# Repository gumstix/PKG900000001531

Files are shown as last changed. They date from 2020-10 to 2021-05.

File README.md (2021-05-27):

# Gumstix Raspberry Pi CM4 + Pixhawk FMUv6
## PKG900000001531 

The **Gumstix Raspberry Pi CM4 + Pixhawk FMUv6** brings together 3 powerful compute devices.  With the Raspberry Pi CM4 module, the Google Coral TPU, and the ST Micro STM32F7 MCU, along with support hardware for MAVs, rovers and other robotics platforms,  designing TensorFlow-assisted autonomous vehicles has never been so accessible.

The *CM4 + Pixhawk FMUv6* is one of the first boards conforming to Pixhawk's v6 specification for Flight Management Units (FMUs), including on-board sensor bank, standard Pixhawk data and power connectors, octal PWM outputs, and firmware support.

The *CM4 + Pixhawk FMUv6* features single-connection programming and debugging.  Power the PCB, flash the CM4's MMC, program the FMU's frimware, or monitor their serial consoles from the same USB Type-C connection.

__Features Include__:
* Raspberry Pi CM4 connector
* Dual Raspberry Pi Camera connectors
* Serial console over USB
* USB Type-C power delivery
* STMicro STM32H753 MCU
* Pixhawk GPS, analog power, RC, and CAN connectors
* 8 PWM outputs
* On-board accelerometer, magnetometer and gyroscope
* On-board barometer
* ASMedia ASM1142 PCIe to USB3.1 controller
* Google Coral G313 TPU (via USB3)

__Links:__
* [AutoDoc Datasheet][autodoc]
* [Specifications][spec]
* [Store Page][store]
* [Schematics and Layout][hardware]

[thumbnail]: about:blank
[autodoc]: PKG900000001531_AutoDoc.pdf
[spec]: PKG900000001531_SpecSheet.pdf
[store]: https://store.gumstix.com/cm4-pixhawk6-mini/
[hardware]: hardware/hardware.md
[firmware]: firmware/firmware.md

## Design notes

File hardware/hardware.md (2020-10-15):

# Hardware

[Schematic PDF][pdf]
EAGLE [Schematic][sch] and [Layout][brd]

[pdf]: PKG900000001531.pdf
[brd]: PKG900000001531.brd
[sch]: PKG900000001531.sch

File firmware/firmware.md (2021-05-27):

# Firmware

## Raspberry Pi OS

* [Raspberry Pi OS (64-bit recommended)](https://downloads.raspberrypi.org/raspios_arm64/images/)
* Username: pi
* Password: raspberry
* Modifications: [config.txt:](config.txt)
```
    # pixhawk
    enable_uart=1
    dtoverlay=dwc2,dr_mode=host
    start_x=1
    gpu_mem=128
    dtoverlay=uart4,ctsrts
    dtoverlay=pcie-32bit-dma
    gpio=6,7=op,dh
```
* Download to /boot folder (first partition) to enable both cameras
    [dt-blob.bin](dt-blob.bin)

## ROS2 Integration

__PX4 Update__:
* Add micrortps client
  * [PX4 1.12.0](px4_fmu-v6u_rtps.px4)
  ```
    FW git-hash: db3c89b1e34af65efc334d928a82196947bd8a3a
    FW version: 1.12.0 80 (17563776)
    FW git-branch: master
  ```
  * Compile with [patch](0001-CM4-micrortps.patch)
  ```
    git am < 0001-CM4-micrortps.patch 
    make px4_fmu-v6u_rtps upload
  ```

__Raspberry Pi CM4 Update__:
* [Install Docker](https://docs.docker.com/engine/install/debian/)
* Add Non-Root User
  ```
    sudo usermod -aG docker ${USER}
  ```
* Enable Docker starting on boot
  ```
    sudo systemctl enable docker
  ```
* Get the image and make it start on boot
  ```
    docker run -d --privileged --net=host --platform=linux/arm64 --restart=always gumstix/px4_ros2
  ```

__[ROS 2 Offboard Control Example](https://docs.px4.io/master/en/ros/ros2_offboard_control.html)__
* Run Docker image on another device on network (can be done on CM4 on Pixhawk).
  * Desktop machine
    ```
      docker run -it --net=host --platform=linux/amd64 gumstix/px4_ros2 bash
    ```
  * Raspberry Pi CM4
    ```
      docker run -it --net=host --platform=linux/arm64 gumstix/px4_ros2 bash
    ```
* Run offboard control example (ros2 is already sourced)
  ```
    ros2 run px4_ros_com offboard_control
  ```

## Coral Accelerator Example
* Install Docker - See above
* Execute steps [1](https://coral.ai/docs/accelerator/get-started/#1-install-the-edge-tpu-runtime), [2](https://coral.ai/docs/accelerator/get-started/#2-install-the-pycoral-library) and [3](https://coral.ai/docs/accelerator/get-started/#3-run-a-model-on-the-edge-tpu) of the [Coral Getting Started](https://coral.ai/docs/accelerator/get-started/)
* Step 3 needs to be run every time before docker command below
* Run gstreamer on host device (ip address = w.x.y.z)
```
  gst-launch-1.0 udpsrc port=5000 ! application/x-rtp,encoding-name=H264,payload=96 ! rtph264depay ! decodebin ! autovideosink
```
* Run Docker image and stream to host device
```
  docker run -d --privileged --network=host gumstix/coral_camera --hostip w.x.y.z
```

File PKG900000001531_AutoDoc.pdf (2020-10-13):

# CM4 Pixhawk 6 Mini

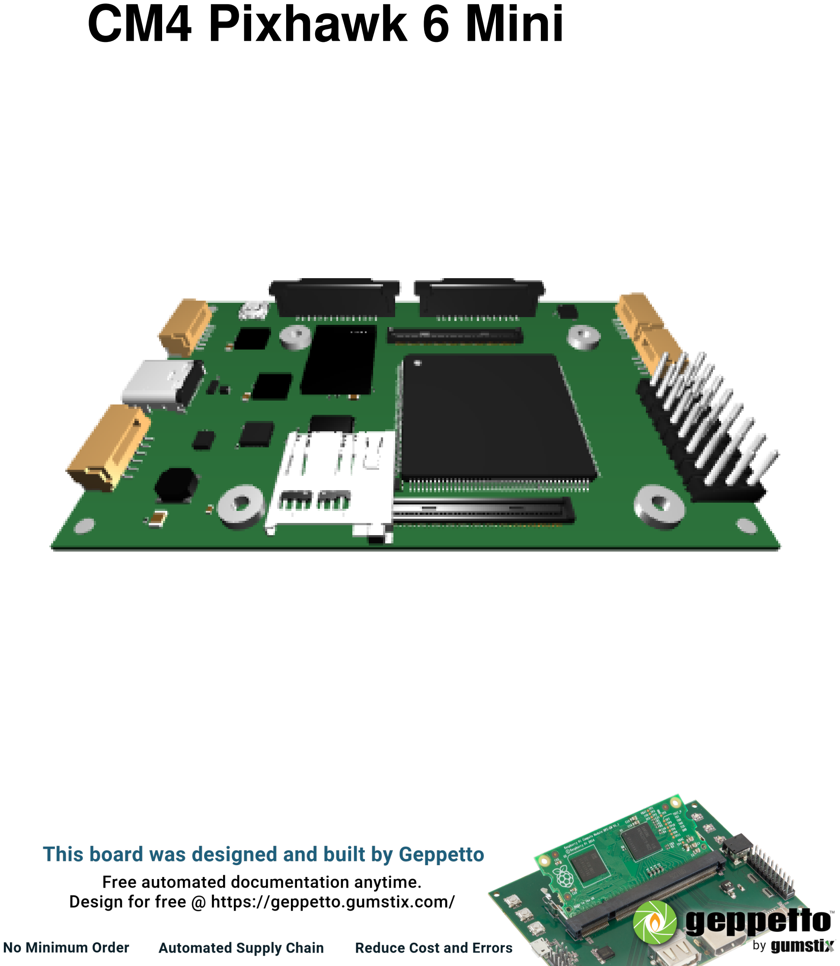
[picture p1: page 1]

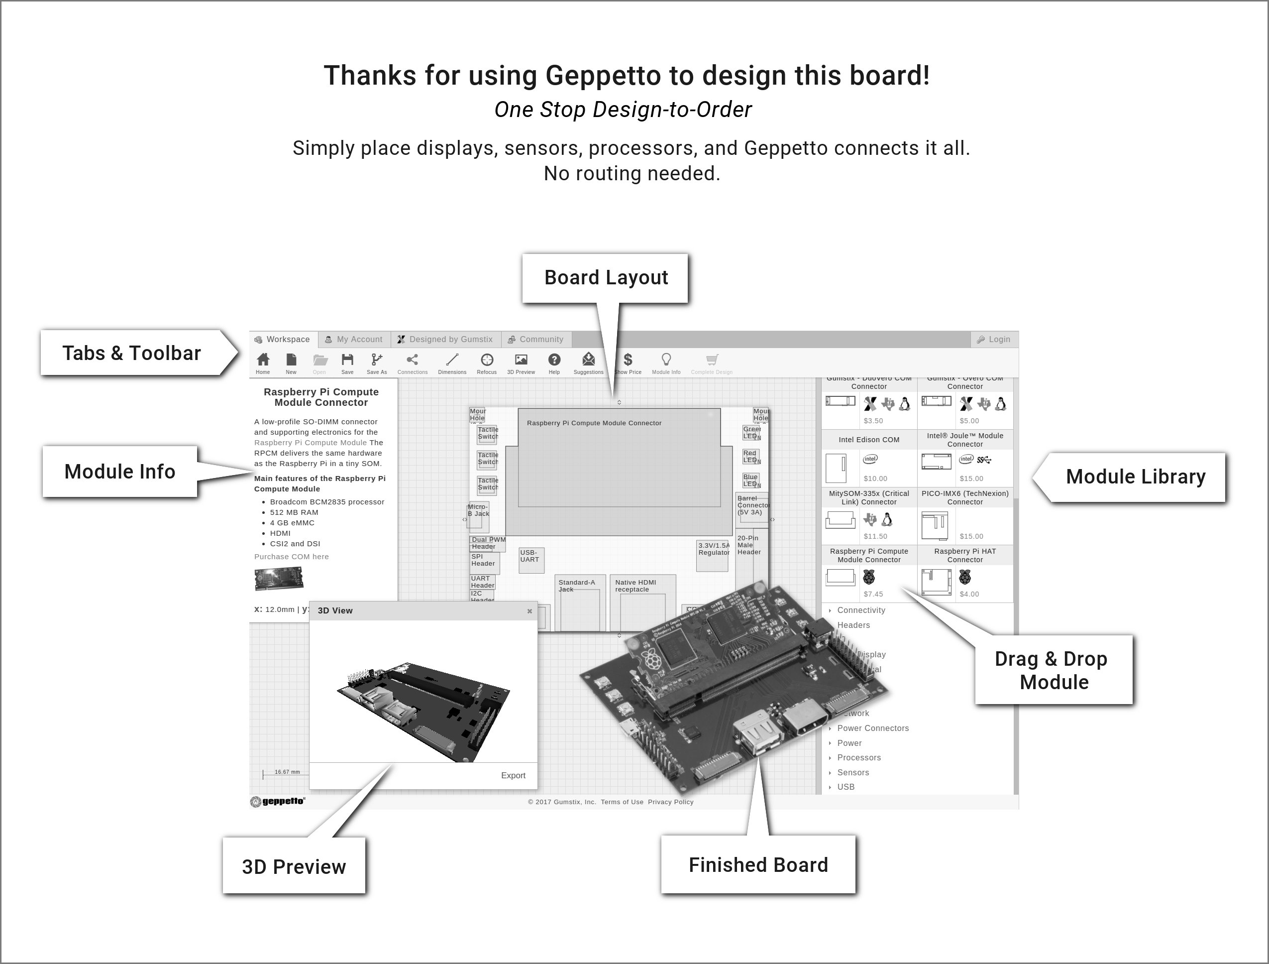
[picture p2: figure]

Gumstix, Inc. shall have no liability of any kind, express or implied, arising out of the use of the Information in this document, including direct, indirect, special or consequential damages.

Gumstix, Inc. may have patents, patent applications, trademarks, copyrights, trade secrets or other intellectual property rights pertaining to Gumstix products described in this document (collectively ”Gumstix Intellectual Property”).

Except as expressly provided in any written license or agreement from Gumstix, Inc., this document and the information contained therein does not create any license to Gumstix’s Intellectual Property.

The Information contained herein is subject to change without notice. Revisions may be issued regarding changes and/or additions.

Copyright

c 2020, Gumstix, Inc. All rights reserved.

## Board Description

Uses Raspberry Pi CM4 Connector as its COM/processor.

Functional modules include:
USB Type-C PD (5V)
3-Port USB Client Hub
USB-UART
USB-UART
USB Type-C PD (5V)
HART Bridge

## Board Dimensions

8cm x 5cm

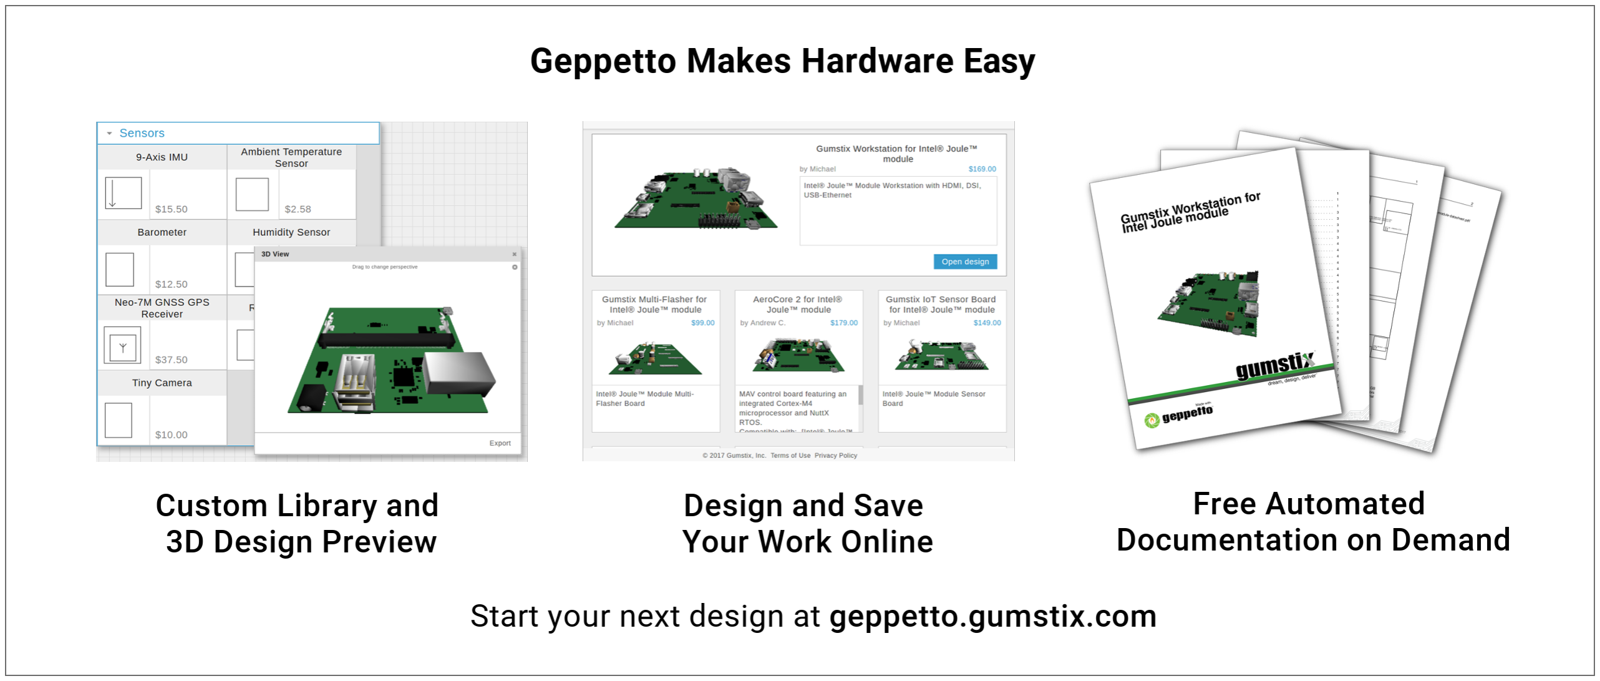
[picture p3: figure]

i

## Contents

1 Modules on Board | 1

ii

CM4 Pixhawk 6 Mini | iii
2 Module Connections Graph | 9
3 Module Power Graph | 10

Revised September 28, 2020

CM4 Pixhawk 6 Mini | 1

## 1 Modules on Board

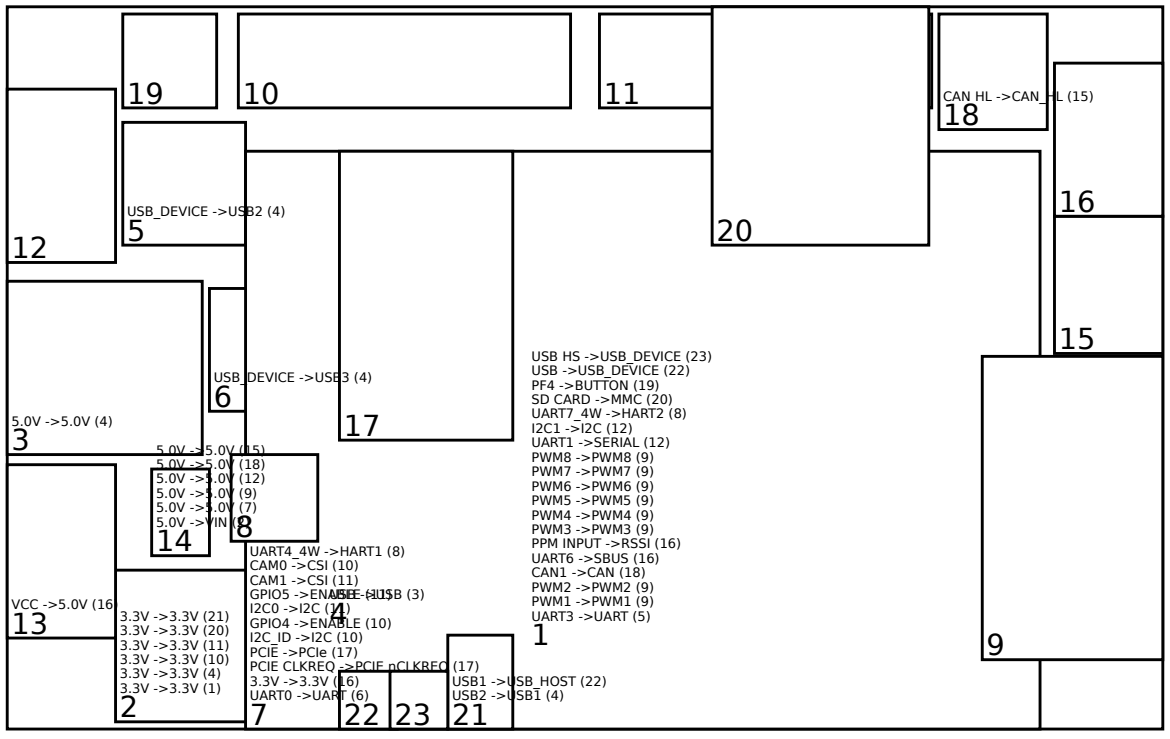
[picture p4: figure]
UART3 ->UART (5); PWM1 ->PWM1 (9); PWM2 ->PWM2 (9); CAN1 ->CAN (18); UART6 ->SBUS (16); PPM INPUT ->RSSI (16); PWM3 ->PWM3 (9); PWM4 ->PWM4 (9); PWM5 ->PWM5 (9); PWM6 ->PWM6 (9); PWM7 ->PWM7 (9); PWM8 ->PWM8 (9); UART1 ->SERIAL (12); UART7_4W ->HART2 (8); SD CARD ->MMC (20); PF4 ->BUTTON (19); USB ->USB_DEVICE (22); USB HS ->USB_DEVICE (23); USB ->USB (3); USB_DEVICE ->USB2 (4); USB_DEVICE ->USB3 (4); UART0 ->UART (6); PCIE CLKREQ ->PCIE nCLKREQ (17); PCIE ->PCIe (17); GPIO4 ->ENABLE (10); GPIO5 ->ENABLE (11); CAM1 ->CSI (11); CAM0 ->CSI (10); UART4_4W ->HART1 (8); VCC ->5.0V (16); 5.0V ->VIN (2); CAN HL ->CAN_HL (15); USB2 ->USB1 (4); USB1 ->USB_HOST (22)

3.3V ->3.3V (21) 3.3V ->3.3V (20) 3.3V ->3.3V (11) 3.3V ->3.3V (10) 3.3V ->3.3V (4) 3.3V ->3.3V (1) 2 | 7

### 1.1 Processors

### 1.1.1 PX4 FMUv6 (v1) (1)

PX4 FMUv6

STM32H753IIT6 is a 32-bit Arm Cortex-M7 core with double precision FPU and L1 cache: 16 Kbytes of data and 16 Kbytes of instruction cache; frequency up to 480 MHz, MPU, 1027 DMIPS/ 2.14 DMIPS/MHz (Dhrystone 2.1), and DSP instructions. It has 2 Mbytes of Flash memory and 1 Mbyte of RAM. Requires:

- 3.3V from 3.3V/1.5A Regulator (2)

Provides:

- UART3 to USB-UART (5)
- PWM1 to Octal PWM Header (9)
- PWM2 to Octal PWM Header (9)
- CAN1 to NXP TJA1051TK/3 CAN Transceiver (18)
- UART6 to Pixhawk RC Input (16)

- PPM INPUT to Pixhawk RC Input (16)
- PWM3 to Octal PWM Header (9)
- PWM4 to Octal PWM Header (9)
- PWM5 to Octal PWM Header (9)
- PWM6 to Octal PWM Header (9)
- PWM7 to Octal PWM Header (9)
- PWM8 to Octal PWM Header (9)
- UART1 to Pixhawk Basic GPS (12)
- I2C1 to Pixhawk Basic GPS (12)
- UART7 4W to HART Bridge (8)
- SD CARD to microSD slot (20)
- PF4 to Tactile Switch (19)
- USB to USB Bridge (22)
- USB HS to USB Bridge (23)

### 1.2 Power

1.2.1 3.3V/1.5A Regulator (v21) (2)

This DC to DC step down regulator provides a 3.3V DC output at 1.5A needed by certain components on this board. It is capable of accepting an input voltage between 3.1 to 16V DC and output is controlled by the TI TPS6211 buck regulator.
It recieves VIN from TI TPS2121 Power Mux (14).

The datasheet for the TPS6211 regulator is available at:

http://www.ti.com/lit/ds/symlink/tps62110.pdf

This regulator provides 3.3V to:

- PX4 FMUv6 (1)
- 3-Port USB Client Hub (4)
- Raspberry Pi Vertical Camera Connector (10)
- Raspberry Pi Vertical Camera Connector (11)
- microSD slot (20)
- USB 2-Port Switch (21)

### 1.2.2 TI TPS2121 Power Mux (v3) (14)

The TI TPS2121 power muxer module transitions between two power sources seamlessly. The au-toswitching power multiplexer ensures power is delivered from the connected source with the highest voltage.

The TPS2121 datasheet is available at:

http://www.ti.com/lit/ds/symlink/tps2121.pdf

This module is not connected.

### 1.3 USB

### 1.3.1 USB Type-C PD (5V) (v1) (3)

A USB Type-C port allows your design to connect as a USB 2.0 and provides up to 3A @ 5.0V.

This port is connected to USB on 3-Port USB Client Hub (4).

1.3.2 3-Port USB Client Hub (v7) (4)

The 3-port USB client hub module offers three interfaces for on-board USB client devices to a single USB device port using the Microchip USB2513 USB 2.0 Hi-speed Hub Controller.

The datasheet for the USB2513 IC is available at:

http://ww1.microchip.com/downloads/en/DeviceDoc/00001692C.pdf

The USB client hub links: USB on USB Type-C PD (5V) (3);
to the following USB device ports:
- USB DEVICE on USB-UART (5)
- USB DEVICE on USB-UART (6)
- USB2 on USB 2-Port Switch (21)

### 1.3.3 USB 2-Port Switch (v1) (21)

USB 2-Port Switch allows the sharing of a single USB 2.0 port.

It requires:

- 3.3V from 3.3V/1.5A Regulator (2)

It provides the following outputs:

- USB2 to 3-Port USB Client Hub (4)
- USB1 to USB Bridge (22)

### 1.4 Converters

### 1.4.1 USB-UART (v21) (5)

Also known as an FTDI, this USB to UART converter allows a USB connection to the board to be-have as a virtual RS232 serial connection. It offers direct and complete access to the system from a development machine by way of the FTDI FT232RQ USB – UART IC.

Technical documentation for the FT232RQ is available at:

http://www.ftdichip.com/Support/Documents/DataSheets/ICs/DS_FT232R.pdf

This USB to UART converter connects a host machine from 3-Port USB Client Hub (4) to UART3 on PX4 FMUv6 (1).

### 1.4.2 USB-UART (v21) (6)

Also known as an FTDI, this USB to UART converter allows a USB connection to the board to be-have as a virtual RS232 serial connection. It offers direct and complete access to the system from a development machine by way of the FTDI FT232RQ USB – UART IC.

Technical documentation for the FT232RQ is available at:

http://www.ftdichip.com/Support/Documents/DataSheets/ICs/DS_FT232R.pdf

This USB to UART converter connects a host machine from 3-Port USB Client Hub (4) to UART0 on Raspberry Pi CM4 Connector (7).

### 1.4.3 HART Bridge (v1) (8)

A HART-HART bridge interfaces two modules with hardware controlled UART lines (e.g., interfacing two processors).

This HART bridge connects UART4 4W on Raspberry Pi CM4 Connector (7) to UART7 4W on PX4 FMUv6 (1).

### 1.4.4 NXP TJA1051TK/3 CAN Transceiver (v2) (18)

The TJA1051TK/3 is a high-speed CAN transceiver that provides an interface between a controller Area Network (CAN) protocol controller and the physical two-wire CAN bus. The transceiver is designed for high-speed CAN applications in the automotive industry, providing differential transmit and receive capability to (a microcontroller with) a CAN protocol controller. The TJA1051TK3 implements the CAN physical layer as defined in ISO 11898-2:2016 and SAE J2284-1 to SAE J2284-5. This implementation enables reliable communication in the CAN FD fast phase at data rates up to 5 Mbit/s. It is suitable for 12 V and 24 V systems. The operating supply voltage of the transceiver is between 4.5V and 5.5V. The module supports IO logic levels of either 3.3V or 5.0V between the controller and transceiver based on the user’s selection while designing on geppetto.

TJA1051TK/3 datasheet:

https://www.nxp.com/docs/en/data-sheet/TJA1051.pdf

This module is connected to CAN1 on PX4 FMUv6 (1).

This module provides the following outputs:

- CAN HL to CAN HL on Pixhawk CAN (15)

### 1.5 COM Connectors

### 1.5.1 Raspberry Pi CM4 Connector (v4) (7)

The Raspberry Pi Compute Module 4 (RPCM4) module contains two connectors to interface with the RPCM4 device. The RPCM4 COM connector is ONLY compatible with the RPCM4.

Technical details for the RPCM modules can be found at:

https://www.raspberrypi.org/documentation/hardware/computemodule/datasheet.md

It requires:

- 5.0V from TI TPS2121 Power Mux (14)

The Geppetto Pi Compute 4 connector provides the following outputs:

- UART0 to USB-UART (6)
- 3.3V to Pixhawk RC Input (16)
- PCIE CLKREQ to Google Coral G313-06329-00 Accelerator (17)
- PCIE to Google Coral G313-06329-00 Accelerator (17)
- I2C ID to Raspberry Pi Vertical Camera Connector (10)
- GPIO4 to Raspberry Pi Vertical Camera Connector (10)
- I2C0 to Raspberry Pi Vertical Camera Connector (11)
- GPIO5 to Raspberry Pi Vertical Camera Connector (11)
- CAM1 to Raspberry Pi Vertical Camera Connector (11)
- CAM0 to Raspberry Pi Vertical Camera Connector (10)
- UART4 4W to HART Bridge (8)

### 1.6 Motors and Relays

### 1.6.1 Octal PWM Header (v11) (9)

This module offers eight PWM headers for controlling servo motors and other PWM-controlled devices.

This header offers PWM outputs connected to:

- PWM1 to PWM1 on PX4 FMUv6 (1)
- PWM2 to PWM2 on PX4 FMUv6 (1)

- PWM3 to PWM3 on PX4 FMUv6 (1)
- PWM4 to PWM4 on PX4 FMUv6 (1)
- PWM5 to PWM5 on PX4 FMUv6 (1)
- PWM6 to PWM6 on PX4 FMUv6 (1)
- PWM7 to PWM7 on PX4 FMUv6 (1)
- PWM8 to PWM8 on PX4 FMUv6 (1)
- 5.0V to 5.0V on TI TPS2121 Power Mux (14)

### 1.7 Connectors (Signal)

### 1.7.1 Raspberry Pi Vertical Camera Connector (v6) (10) — CAM0

The Raspberry Pi Vertical camera connector module is a 15-pin ribbon connector that exposes a 2-lane MIPI camera system to an external high-resolution camera module.

The CSI port is connected to CAM0 on Raspberry Pi CM4 Connector (7).

I2C communication is connected to I2C ID on Raspberry Pi CM4 Connector (7).

ENABLE input provided by GPIO4 on Raspberry Pi CM4 Connector (7).

### 1.7.2 Raspberry Pi Vertical Camera Connector (v6) (11) — CAM1

The Raspberry Pi Vertical camera connector module is a 15-pin ribbon connector that exposes a 2-lane MIPI camera system to an external high-resolution camera module.

The CSI port is connected to CAM1 on Raspberry Pi CM4 Connector (7).

I2C communication is connected to I2C0 on Raspberry Pi CM4 Connector (7).

ENABLE input provided by GPIO5 on Raspberry Pi CM4 Connector (7).

### 1.7.3 USB Bridge (v9) (22)

The USB bridge connects PX4 FMUv6 (1) to USB 2-Port Switch (21) as a USB device.

### 1.7.4 USB Bridge (v9) (23)

The USB bridge connects PX4 FMUv6 (1) to as a USB device.

### 1.8 Custom Modules

### 1.8.1 Pixhawk Basic GPS (v3) (12)

The custom 6-pin JST GH header offers up to 6 pins that can be used at the customer’s discretion.

This module has the following connections:

- SERIAL to UART1 from PX4 FMUv6 (1)
- I2C to I2C1 from PX4 FMUv6 (1)
- 5.0V to 5.0V from TI TPS2121 Power Mux (14)

### 1.8.2 Pixhawk Analog Power (v3) (13)

The custom 6-pin JST GH header offers up to 6 pins that can be used at the customer’s discretion.

This module is not connected.

### 1.8.3 Pixhawk CAN (v6) (15)

The custom 4-pin JST GH header offers up to 4 pins that can be used at the customer’s discretion.

This module has the following connections:

- 5.0V to 5.0V from TI TPS2121 Power Mux (14)
- CAN HL to CAN HL from NXP TJA1051TK/3 CAN Transceiver (18)

•

### 1.8.4 Pixhawk RC Input (v4) (16)

The custom 5-pin JST GH header offers up to 5 pins that can be used at the customer’s discretion.

This module has the following connections:

- SBUS to UART6 from PX4 FMUv6 (1)
- RSSI to PPM INPUT from PX4 FMUv6 (1)
- 3.3V to 3.3V from Raspberry Pi CM4 Connector (7)
- 5.0V to VCC from Pixhawk Analog Power (13)

### 1.9 Sensors

### 1.9.1 Google Coral G313-06329-00 Accelerator (v2) (17)

The Google Coral Accelerator Module is a multi-chip module (MCM) that includes the Edge TPU and its own power control. The Edge TPU is a small ASIC designed by Google that accelerates Tensor

Flow Lite models using little power: it’s capable of performing 4 trillion operations per second (4 TOPS), using 2 watts of powerthat’s 2 TOPS per watt. For example, it can execute state-of-the-art mobile vision models such as MobileNet v2 at almost 400 frames per second, in a power efficient manner. This on-device ML processing reduces latency, increases data privacy, and removes the need for a constant internet connection. The module provides either of the host interface i.e. PCIe Gen2 x 1 or USB2.0.

The datasheet for the G313-06329-00 module is available at:

https://coral.ai/static/files/Coral-Accelerator-Module-datasheet.pdf

The module connects to the following buses:

- PCIE nCLKREQ to PCIE CLKREQ on Raspberry Pi CM4 Connector (7)
- VLOGIC PCIE CTRL to VLOGIC on Raspberry Pi CM4 Connector (7)
- PCIe to PCIE on Raspberry Pi CM4 Connector (7)

•

### 1.10 Lights and Switches

### 1.10.1 Tactile Switch (v22) (19) — RESET

This 4.9 sq. mm pull-down touch switch provides a user input for the signal PF4 on PX4 FMUv6 (1).

### 1.11 Memory

### 1.11.1 microSD slot (v16) (20)

The Micro SD card slot module provides removable non-volatile memory to Geppetto designs.

The SD card reader is connected to SD CARD on PX4 FMUv6 (1).

## 2 Module Connections Graph

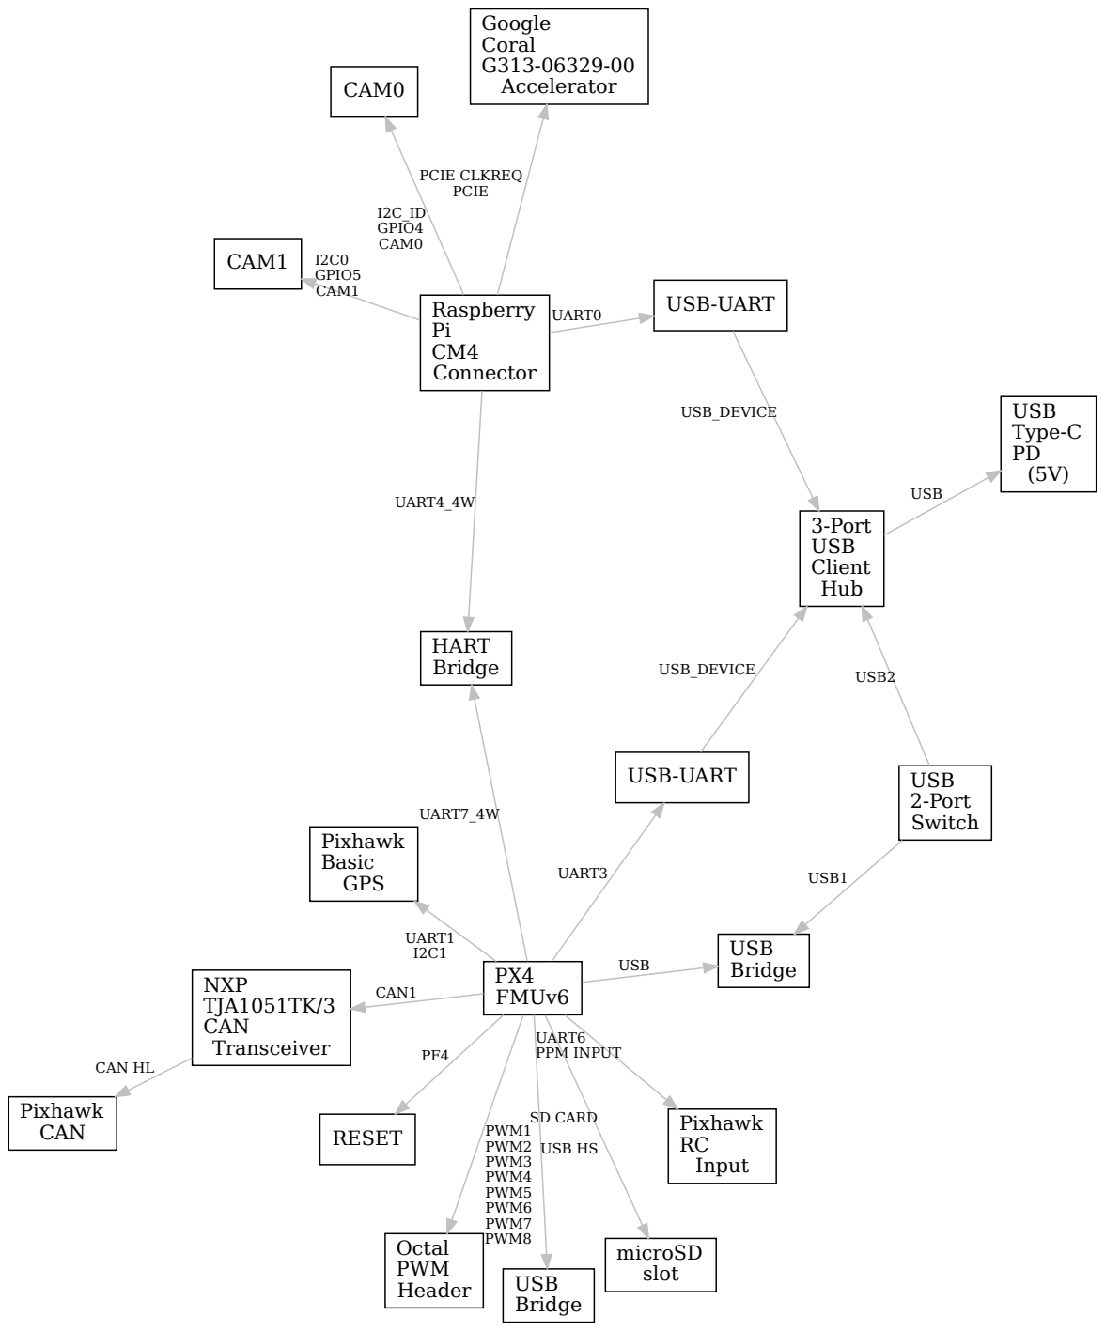
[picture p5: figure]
PX4 FMUv6; USB-UART; UART3; Octal PWM Header; PWM1 PWM2 PWM3 PWM4 PWM5 PWM6 PWM7 PWM8; NXP TJA1051TK/3 CAN Transceiver; CAN1; Pixhawk RC Input; UART6 PPM INPUT; Pixhawk Basic GPS; UART1 I2C1; HART Bridge; UART7_4W; microSD slot; SD CARD; RESET; USB Bridge USB; USB Bridge; USB HS; 3-Port USB Client Hub; USB_DEVICE; Pixhawk CAN; CAN HL; USB Type-C PD (5V); USB; USB 2-Port Switch; USB1; USB2; Raspberry Pi CM4 Connector; UART4_4W; UART0; Google Coral G313-06329-00 Accelerator; PCIE CLKREQ PCIE; CAM0; I2C_ID GPIO4 CAM0; CAM1; GPIO5 CAM1

Figure 1: excludes power modules

## 3 Module Power Graph

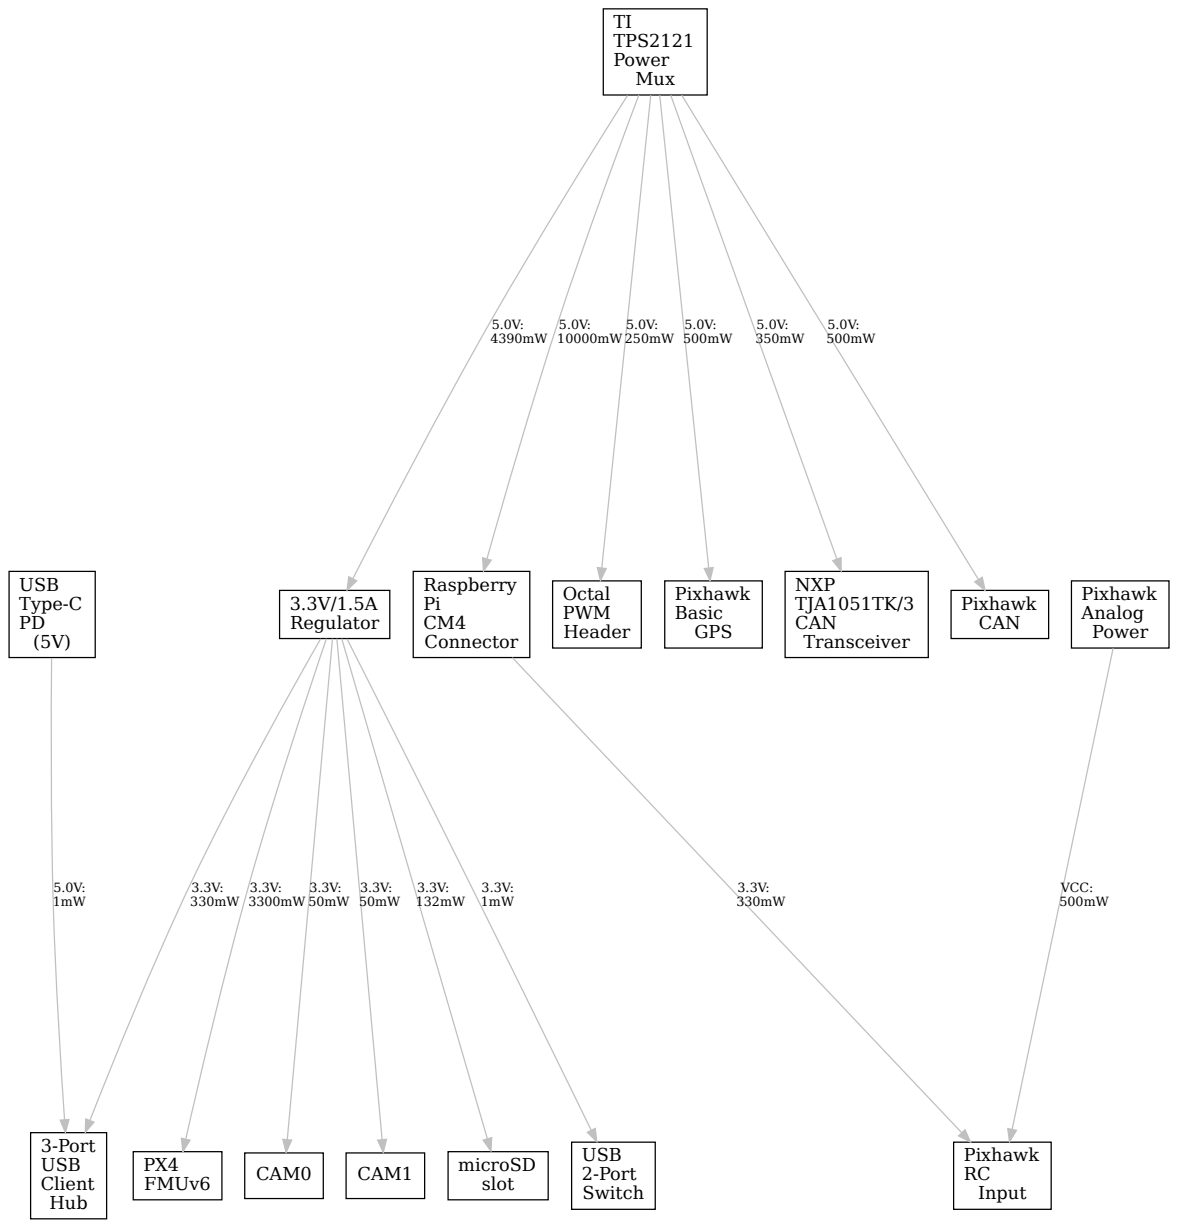
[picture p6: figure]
3.3V/1.5A Regulator; PX4 FMUv6; 3-Port USB Client Hub; CAM0; CAM1; microSD slot; USB 2-Port Switch; TI TPS2121 Power Mux; Raspberry Pi CM4 Connector; Octal PWM Header; Pixhawk Basic GPS; NXP TJA1051TK/3 CAN Transceiver; Pixhawk CAN; USB Type-C PD (5V); Pixhawk RC Input; Pixhawk Analog Power; VCC: 500mW

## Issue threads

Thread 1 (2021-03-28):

Flashing the CM4

nilay994, 2021-03-28:
Thanks for the nice board @Gumstix!

Questions related to getting started with the Gumstix Raspberry Pi CM4:

1. Can the eMMC of CM4 be flashed directly after being mounted to the Gumstix Board? In other words, can the USB-C connector of the gumstix disable the eMMC boot and force the RPi to boot in the flashing mode?
2. I see "This USB to UART converter connects a host machine from 3-Port USB Client Hub (4) to UART0 on Raspberry Pi CM4 Connector (7)." Is this dependent on the three positions that a switch can be in, next to the USB hub? The USB hub looks really nice, since it exposes multiple UARTs of the STM and RPi at one port. Could there be more verbose statements about the USB hub? Would love to be able to use this multi-channel functionality more frequently.
3. Can there be more verbose documentation of the connection between the STM32 and the CM4? Are these interfaces completely accessible to the user? or are they locked by some application running on the CM4?
4. What is the difference between the RPi image provided [here](https://github.com/gumstix/PKG900000001531/blob/master/firmware/firmware.md) and the default image? Is it just the device tree reference file?

patrickpoirier51, 2021-03-28:
Hello,

Funny, I received the board last week and stated working on this by the time you opened issue :-)...
I loaded the UBUNTU image using the Compute Module IO board and it worke flawlessly.
It is mapping  a com port on the USB c and output MAVLINK @ 57600bps

Hope it helps

smithandrewc, 2021-03-30:
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
Not on this version.  We're building a new version of the board that will allow this.

> 2. I see "This USB to UART converter connects a host machine from 3-Port USB Client Hub (4) to UART0 on Raspberry Pi CM4 Connector (7)." Is this dependent on the three positions that a switch can be in, next to the USB hub? The USB hub looks really nice, since it exposes multiple UARTs of the STM and RPi at one port. Could there be more verbose statements about the USB hub? Would love to be able to use this multi-channel functionality more frequently.
This puts module puts out the default (UART0) console through an FTDI USB-UART port and is connected to the USB hub, accessible through the Type-C connector.  No switches are necessary, the CM4 console, FMU console and FMU USB bus are all available through the Type-C connector.
> 3. Can there be more verbose documentation of the connection between the STM32 and the CM4? Are these interfaces completely accessible to the user? or are they locked by some application running on the CM4?
The schematic for the board is available here, what additional documentation do you require?  The CM4 and STM32 are connected through a UART channel only (the default TELEM2 channel on FMU).
> 4. What is the difference between the RPi image provided [here](https://github.com/gumstix/PKG900000001531/blob/master/firmware/firmware.md) and the default image? Is it just the device tree reference file?
What "default image" are you referring to?

nilay994, 2021-03-31:
> The CM4 and STM32 are connected through a UART channel only (the default TELEM2 channel on FMU).

The USB-C hub is nice and versatile :) Found the channel in the schematics pdf, thank you for providing the reference. Planning to tap into these UART lines serving as a test point, can solder wires on to the 0R resistor.

> What "default image" are you referring to?

I could have been clearer. With default image, I meant the Raspberry Pi OS/Raspbian or the image that RPi flashing tool uses for getting started with the CM4.

Closed 2021-04-05.

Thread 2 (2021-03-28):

UBUNTU source & framework

patrickpoirier51, 2021-03-28:
Hello,

I just loaded the UBUNTU image and it work ok with PX4.

My goal is to make an image for ArduPilot and not wanting to reinvent the wheel, I would need detailled information on the different modules used (if any), specific mappings of peripherals, config files and startup scripts.

Regards

patrickpoirier51, 2021-03-29:
Well... in the meantime I think I'll dig into it ;-)

--First issue Pi is not showing on third USB mapping

I could see Mavlink on first USB and PX4 Shell on second USB, but no RPI login on third.
Her's what I dis to correct:

`/boot/firmware/config.txt
enable_uart=1

/boot/firmware/syscfg.txt
#cmdline=cmdline.txt
cmdline=cmdline.txt.serial

at cmdline.txt.serial
net.ifnames=0 dwc_otg.lpm_enable=0 console=serial0,115200 console=tty1 root=LABEL=writable rootfstype=ext4 elevator=deadline rootwait fixrtc

remove symlink on rc.local == I want a direct link to the port
cat rc.local
#!/bin/bash
#ln -s /dev/ttyAMA1 /dev/ttyS0
`

--

Then ENABLE WIFI
ENABLE WIFI
https://linuxconfig.org/ubuntu-20-04-connect-to-wifi-from-command-line

ENABLE SSH
https://linuxize.com/post/how-to-enable-ssh-on-ubuntu-20-04/

reboot then  ssh ubuntu on WIFI address  with raspberry as password

now we have access to internet and  we can update , add tools ... whatever
 !!! Issue while building packages =
`update-initramfs: Generating /boot/initrd.img-5.4.0-1021-raspi
Unsupported platform.
run-parts: /etc/initramfs/post-update.d//flash-kernel exited with return code 1
dpkg: error processing package initramfs-tools (--configure):
 installed initramfs-tools package post-installation script subprocess returned error exit status 1
Errors were encountered while processing:
 initramfs-tools
`

But the installed packages seems to work ok ... so far :-)

Finally install MAVPROXY

Install MAVPROXY
pip install PyYAML mavproxy --user

echo "export PATH=$PATH:$HOME/.local/bin" >> ~/.bashrc
source ~/.bashrc

 mavproxy.py --master=/dev/ttyAMA1 --baudrate=921600 --out=udpout: "toGCS:14550

Enjoy,  Regards

smithandrewc, 2021-03-29:
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

Autopilot was built to conform to Pixhawk FMUv6U standard. Spec should have been published by now but I don't see it. All board support has been added to mainline PX4. All hardware documents have been uploaded here.

What else are you looking for?

smithandrewc, 2021-03-29:
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

I believe only change required to get console is setting enable_uart=1.

Have you tried mainline Raspberry Pi OS? That works as well.

patrickpoirier51, 2021-03-29:
Hello,

Thanks for getting back so rapidly :-)

Concerning uart access , is this mapping  really required then ?
ln -s /dev/ttyAMA1 /dev/ttyS0

Has the mainline Raspberry Pi OS has access to the CORAL chip ?

Regards,

smithandrewc, 2021-03-29:
I don't see why that mapping would be required.

Coral chip is USB, software support is identical to USB Accelerator

https://coral.ai/docs/accelerator/get-started/

patrickpoirier51, 2021-03-29:
Ahhh cool , I thought it was deeply interconnected with GPIOS as described here:
**Gumstix Raspberry Pi CM4 + Pixhawk FMUv6   page 8**

The module connects to the following buses:
• PCIE nCLKREQ to PCIE CLKREQ on Raspberry Pi CM4 Connector (7)
• VLOGIC PCIE CTRL to VLOGIC on Raspberry Pi CM4 Connector (7)
• PCIe to PCIE on Raspberry Pi CM4 Connector (7)

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

patrickpoirier51, 2021-03-29:
and lsusb doe not show much

Bus 001 Device 001: ID 1d6b:0002 Linux Foundation 2.0 root hub
ubuntu@ubuntu:~$ Bus 001 Device 001: ID 1d6b:0002 Linux Foundation 2.0 root hub

patrickpoirier51, 2021-03-30:
OK, double check with schematic and yeah.... it is USB only

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

patrickpoirier51, 2021-03-30:
@smithandrewc  I think the documentation would  need to be more explicit....
Now question: How do we access the TPU ?

patrickpoirier51, 2021-03-30:
I cannot see the Google Coral on the Gumstix
It works OK on the CM IO Board with a CORAL stick plugged in USB

Any guidance ?

smithandrewc, 2021-03-30:
Early test boards had an issue with the Coral device, we've addressed it in our newest build.

patrickpoirier51, 2021-03-30:
@smithandrewc  there are other issues in this thread, I guess you will fix that ?

One other thing
it looks like you somehow installed an older version of tflite_runtime, the version should have returned 2.5:
python3 -c 'print(__import__("tflite_runtime").__version__)'
2.5.0

sudo pip3 remove tflite-runtime == it was 2.1
and reinstall with apt

smithandrewc, 2021-03-30:
What other issues? This Ubuntu image is the original one we deployed with the CM4 before there was mainline support. I would recommend using a new image. We will be removing this image soon.

patrickpoirier51, 2021-03-31:
The nonexistent  mapping of the Pi  console on USB
The outdated python library
The misguiding documentation

An I might add
The undocumented method to flash the firmware
The lack of transparence on a major issue with the Beta Units....

Le mar. 30 mars 2021 à 19:12, Andrew C. Smith ***@***.***> a
écrit :

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

patrickpoirier51, 2021-03-31:
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

This is misleading as the final design is purely USB

smithandrewc, 2021-03-31:
> I mean flashing the firmware on the STM32

This is a mainline supported PX4 board.  Flashing it follows the same routine as all the other PX4 boards (QGroundcontrol or via source code).

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

This is a good point, that is confusing.  We'll fix it, thanks for pointing it out.

patrickpoirier51, 2021-03-31:
You are welcome :-)

Closed 2021-03-30.

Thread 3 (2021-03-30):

USB Lines Criss-Cross Fix is not Working

patrickpoirier51, 2021-03-30:
The Coral chip is not detected on my Gumstix Raspberry Pi CM4 + Pixhawk FMUv6.

After having exhausted all the software and configuration issues, I decided to test on the CM4 IO board with my own Coral USB stick and all worked OK.

This is when I decided to investigate this hardware rework on the USB lines
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

Being a criss-cross it appear that the runs had to be cut.... and its not the case.
So I cut them:
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

Now I can see the USB device:
dmesg | grep usb
New USB device found, idVendor=1d6b, idProduct=0002, bcdDevice= 5.04
lsusb
Bus 001 Device 002: ID 1a6e:089a Global Unichip Corp.
Bus 001 Device 001: ID 1d6b:0002 Linux Foundation 2.0 root hub

But when I launch the test , the python test start but it never finalise the test  with sporadic bus speed errors messages on terminal.

Conclusion: This quick fix does not work properly as it expose and unbalance the USB data lines.

patrickpoirier51, 2021-04-15:
Hello,  When are yyou planning to release the new boards sowe can finish the ArduPilot integration ?

smithandrewc, 2021-04-15:
We're building a new version now. However, it is only making changes to the CM4 and Coral. How does this affect Ardupilot?

patrickpoirier51, 2021-04-15:
I am taking part of the CM4 integration, so I need a fully functionnal unit in order to build a complete image.

smithandrewc, 2021-04-16:
Well unfortunately due to scarcity of parts, I don't expect us to have a decent volume of these for a couple of months.  I would recommend you get a hold of an external USB coral device and CM4 board and do whatever testing you can.

Alternatively, you get get one of our Uprev AI and CM Robo boards
https://www.gumstix.com/cm4-uprev-ai.html
https://www.gumstix.com/cm-robo.html
Put the CM4 on the Uprev AI and into the Robo board end either connect the UART header on the Robo to GPS header on the Pixhawk or use the USB ports on the two boards.  It'll require some minor changes to get the MAVLink data on those channels but would get you as close as possible to the finished board.  If you're interested in pursuing either avenue, get a hold of our customer support.

mariorra, 2021-08-17:
Hi Guys! Thanks for sharing this issue

I arrive here bc I'm working on a solution that provides something similar. But let see that it is something there that makes me confuse.
The Version that I have is the 4. There the schematic shows the following connection. I wrote by hand the red lines to define what was the issue in the past.

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

My confusion is if I follow the connection between the ASM1142 and CORAL:

ASM1142                     LABEL                             LABEL             CORAL
USB1_SSTX_P PIN42    USB1_SSTX_P   -->    USB1_SSTX_N   PCIE_RX_P
USB1_SSTX_N PIN43   USB1_SSTX_N  -->     USB1_SSTX_P    PCIE_RX_N

Is the issue fixed on the side of the labels?
Do I have to follow the labels in order to have a good connection using the guidelines that google provides?

Thanks in advance

smithandrewc, 2021-08-17:
The initial post in this thread was in regards to the error in swapping the polarity of the USB2 signals.  That has been fixed.  Your question about swapping the polarity of the SSTX lines is intentional.  The superspeed signals allow for polarity inversion to allow for better routing (i.e. not using vias).  We made use of that.

mariorra, 2021-08-17:
Ok, great. Thanks for the answer. Do you have any other comments that avoid to waste the time and money according to your experience with both modules?

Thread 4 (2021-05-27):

REV4 board issue with ASM1442K chip overheating

patrickpoirier51, 2021-05-27:
Hello,

I just received the new V4 release for testing.
Just connected to USB C Raspberry Pi Power supply and after a few swconds the  ASM1442K chip is overheating ( I mean boiling hot), is this expected ?
It seems like there  is a shortcircuit somewhere.

Anyway, I put the CM4 just for checking and  here is dmesg (of the UBUNTU image ) in case it might help:

dmesg
[    0.000000] Booting Linux on physical CPU 0x0000000000 [0x410fd083]
[    0.000000] Linux version 5.4.0-1015-raspi (buildd@bos02-arm64-074) (gcc version 9.3.0 (Ubuntu 9.3.0-10ubuntu2)) #15-Ubuntu SMP Fri Jul 10 05:34:24 UTC 2020 (Ubuntu 5.4.0-1015.15-raspi 5.4.44)
[    0.000000] Machine model: Raspberry Pi Compute Module 4 Rev 1.0
[    0.000000] efi: Getting EFI parameters from FDT:
[    0.000000] efi: UEFI not found.
[    0.000000] Reserved memory: created CMA memory pool at 0x000000002c000000, size 64 MiB
[    0.000000] OF: reserved mem: initialized node linux,cma, compatible id shared-dma-pool
[    0.000000] On node 0 totalpages: 491520
[    0.000000]   DMA zone: 3584 pages used for memmap
[    0.000000]   DMA zone: 0 pages reserved
[    0.000000]   DMA zone: 229376 pages, LIFO batch:63
[    0.000000]   DMA32 zone: 4096 pages used for memmap
[    0.000000]   DMA32 zone: 262144 pages, LIFO batch:63
[    0.000000] percpu: Embedded 32 pages/cpu s92120 r8192 d30760 u131072
[    0.000000] pcpu-alloc: s92120 r8192 d30760 u131072 alloc=32*4096
[    0.000000] pcpu-alloc: [0] 0 [0] 1 [0] 2 [0] 3
[    0.000000] Detected PIPT I-cache on CPU0
[    0.000000] CPU features: detected: EL2 vector hardening
[    0.000000] CPU features: kernel page table isolation forced ON by KASLR
[    0.000000] CPU features: detected: Kernel page table isolation (KPTI)
[    0.000000] ARM_SMCCC_ARCH_WORKAROUND_1 missing from firmware
[    0.000000] Built 1 zonelists, mobility grouping on.  Total pages: 483840
[    0.000000] Kernel command line:  coherent_pool=1M 8250.nr_uarts=1 snd_bcm2835.enable_compat_alsa=0 snd_bcm2835.enable_hdmi=1 snd_bcm2835.enable_headphones=1 bcm2708_fb.fbwidth=0 bcm2708_fb.fbheight=0 bcm2708_fb.fbswap=1 smsc95xx.macaddr=DC:A6:32:FE:7E:DA vc_mem.mem_base=0x3ec00000 vc_mem.mem_size=0x40000000  net.ifnames=0 dwc_otg.lpm_enable=0 console=ttyS0,115200 console=tty1 root=LABEL=writable rootfstype=ext4 elevator=deadline rootwait fixrtc quiet splash
[    0.000000] Dentry cache hash table entries: 262144 (order: 9, 2097152 bytes, linear)
[    0.000000] Inode-cache hash table entries: 131072 (order: 8, 1048576 bytes, linear)
[    0.000000] mem auto-init: stack:off, heap alloc:off, heap free:off
[    0.000000] software IO TLB: mapped [mem 0x34000000-0x38000000] (64MB)
[    0.000000] Memory: 1738900K/1966080K available (11772K kernel code, 1236K rwdata, 4244K rodata, 6144K init, 1072K bss, 161644K reserved, 65536K cma-reserved)
[    0.000000] random: get_random_u64 called from kmem_cache_open+0x38/0x3e0 with crng_init=0
[    0.000000] SLUB: HWalign=64, Order=0-3, MinObjects=0, CPUs=4, Nodes=1
[    0.000000] ftrace: allocating 38984 entries in 153 pages
[    0.000000] rcu: Hierarchical RCU implementation.
[    0.000000]  Tasks RCU enabled.
[    0.000000] rcu: RCU calculated value of scheduler-enlistment delay is 25 jiffies.
[    0.000000] NR_IRQS: 64, nr_irqs: 64, preallocated irqs: 0
[    0.000000] GIC: Using split EOI/Deactivate mode
[    0.000000] arch_timer: cp15 timer(s) running at 54.00MHz (phys).
[    0.000000] clocksource: arch_sys_counter: mask: 0xffffffffffffff max_cycles: 0xc743ce346, max_idle_ns: 440795203123 ns
[    0.000006] sched_clock: 56 bits at 54MHz, resolution 18ns, wraps every 4398046511102ns
[    0.000205] Console: colour dummy device 80x25
[    0.000228] printk: console [tty1] enabled
[    0.000277] Calibrating delay loop (skipped), value calculated using timer frequency.. 108.00 BogoMIPS (lpj=216000)
[    0.000291] pid_max: default: 32768 minimum: 301
[    0.000504] LSM: Security Framework initializing
[    0.000553] Yama: becoming mindful.
[    0.000642] AppArmor: AppArmor initialized
[    0.000836] Mount-cache hash table entries: 4096 (order: 3, 32768 bytes, linear)
[    0.000867] Mountpoint-cache hash table entries: 4096 (order: 3, 32768 bytes, linear)
[    0.000934] *** VALIDATE tmpfs ***
[    0.001562] *** VALIDATE proc ***
[    0.002087] Disabling memory control group subsystem
[    0.002158] *** VALIDATE cgroup1 ***
[    0.002168] *** VALIDATE cgroup2 ***
[    0.003393] ASID allocator initialised with 32768 entries
[    0.003559] rcu: Hierarchical SRCU implementation.
[    0.005651] EFI services will not be available.
[    0.006475] smp: Bringing up secondary CPUs ...
[    0.007346] Detected PIPT I-cache on CPU1
[    0.007399] CPU1: Booted secondary processor 0x0000000001 [0x410fd083]
[    0.008462] Detected PIPT I-cache on CPU2
[    0.008499] CPU2: Booted secondary processor 0x0000000002 [0x410fd083]
[    0.009474] Detected PIPT I-cache on CPU3
[    0.009510] CPU3: Booted secondary processor 0x0000000003 [0x410fd083]
[    0.009653] smp: Brought up 1 node, 4 CPUs
[    0.009662] SMP: Total of 4 processors activated.
[    0.009671] CPU features: detected: 32-bit EL0 Support
[    0.009681] CPU features: detected: CRC32 instructions
[    0.017299] CPU features: emulated: Privileged Access Never (PAN) using TTBR0_EL1 switching
[    0.017308] CPU: All CPU(s) started at EL2
[    0.017382] alternatives: patching kernel code
[    0.018895] devtmpfs: initialized
[    0.028409] Enabled cp15_barrier support
[    0.028434] Enabled setend support
[    0.028909] clocksource: jiffies: mask: 0xffffffff max_cycles: 0xffffffff, max_idle_ns: 7645041785100000 ns
[    0.028932] futex hash table entries: 1024 (order: 4, 65536 bytes, linear)
[    0.031130] pinctrl core: initialized pinctrl subsystem
[    0.031753] DMI not present or invalid.
[    0.032459] NET: Registered protocol family 16
[    0.034890] DMA: preallocated 1024 KiB pool for atomic allocations
[    0.034908] audit: initializing netlink subsys (disabled)
[    0.035161] audit: type=2000 audit(0.032:1): state=initialized audit_enabled=0 res=1
[    0.035688] cpuidle: using governor ladder
[    0.035722] cpuidle: using governor menu
[    0.036244] hw-breakpoint: found 6 breakpoint and 4 watchpoint registers.
[    0.036542] Serial: AMBA PL011 UART driver
[    0.039287] bcm2835-mbox fe00b880.mailbox: mailbox enabled
[    0.052133] raspberrypi-firmware soc:firmware: Attached to firmware from 2020-07-02 15:00, variant start_x
[    0.056142] raspberrypi-firmware soc:firmware: Firmware hash is 36c8be9515deddc9d2b1f469374f00d0a2df13f9
[    0.107241] bcm2835-dma fe007000.dma: DMA legacy API manager, dmachans=0x1
[    0.110060] iommu: Default domain type: Translated
[    0.111219] SCSI subsystem initialized
[    0.111459] libata version 3.00 loaded.
[    0.111648] usbcore: registered new interface driver usbfs
[    0.111691] usbcore: registered new interface driver hub
[    0.111786] usbcore: registered new device driver usb
[    0.112147] pps_core: LinuxPPS API ver. 1 registered
[    0.112155] pps_core: Software ver. 5.3.6 - Copyright 2005-2007 Rodolfo Giometti <giometti@linux.it>
[    0.112172] PTP clock support registered
[    0.112438] EDAC MC: Ver: 3.0.0
[    0.113671] NetLabel: Initializing
[    0.113680] NetLabel:  domain hash size = 128
[    0.113686] NetLabel:  protocols = UNLABELED CIPSOv4 CALIPSO
[    0.113764] NetLabel:  unlabeled traffic allowed by default
[    0.114655] clocksource: Switched to clocksource arch_sys_counter
[    0.196883] *** VALIDATE bpf ***
[    0.197291] VFS: Disk quotas dquot_6.6.0
[    0.197379] VFS: Dquot-cache hash table entries: 512 (order 0, 4096 bytes)
[    0.197491] *** VALIDATE ramfs ***
[    0.198053] AppArmor: AppArmor Filesystem Enabled
[    0.207438] thermal_sys: Registered thermal governor 'fair_share'
[    0.207443] thermal_sys: Registered thermal governor 'bang_bang'
[    0.207452] thermal_sys: Registered thermal governor 'step_wise'
[    0.207459] thermal_sys: Registered thermal governor 'user_space'
[    0.207467] thermal_sys: Registered thermal governor 'power_allocator'
[    0.207982] NET: Registered protocol family 2
[    0.208653] tcp_listen_portaddr_hash hash table entries: 1024 (order: 2, 16384 bytes, linear)
[    0.208690] TCP established hash table entries: 16384 (order: 5, 131072 bytes, linear)
[    0.208792] TCP bind hash table entries: 16384 (order: 6, 262144 bytes, linear)
[    0.209024] TCP: Hash tables configured (established 16384 bind 16384)
[    0.209213] UDP hash table entries: 1024 (order: 3, 32768 bytes, linear)
[    0.209245] UDP-Lite hash table entries: 1024 (order: 3, 32768 bytes, linear)
[    0.209462] NET: Registered protocol family 1
[    0.209488] NET: Registered protocol family 44
[    0.209503] PCI: CLS 0 bytes, default 64
[    0.209743] Trying to unpack rootfs image as initramfs...
[    0.845343] Freeing initrd memory: 28836K
[    0.847008] hw perfevents: enabled with armv8_cortex_a72 PMU driver, 7 counters available
[    0.847215] kvm [1]: IPA Size Limit: 44bits
[    0.848112] kvm [1]: vgic interrupt IRQ1
[    0.848332] kvm [1]: Hyp mode initialized successfully
[    0.850492] Initialise system trusted keyrings
[    0.850542] Key type blacklist registered
[    0.850860] workingset: timestamp_bits=46 max_order=19 bucket_order=0
[    0.857464] zbud: loaded
[    0.859430] squashfs: version 4.0 (2009/01/31) Phillip Lougher
[    0.860436] fuse: init (API version 7.31)
[    0.860555] *** VALIDATE fuse ***
[    0.860567] *** VALIDATE fuse ***
[    0.893262] Key type asymmetric registered
[    0.893273] Asymmetric key parser 'x509' registered
[    0.893335] Block layer SCSI generic (bsg) driver version 0.4 loaded (major 242)
[    0.893571] io scheduler mq-deadline registered
[    0.897818] brcm-pcie fd500000.pcie: host bridge /scb/pcie@7d500000 ranges:
[    0.897837] brcm-pcie fd500000.pcie:   No bus range found for /scb/pcie@7d500000, using [bus 00-ff]
[    0.897884] brcm-pcie fd500000.pcie:      MEM 0x0600000000..0x0603ffffff -> 0x00f8000000
[    0.897930] brcm-pcie fd500000.pcie:   IB MEM 0x0000000000..0x007fffffff -> 0x0000000000
[    0.944750] brcm-pcie fd500000.pcie: link up, 5 GT/s x1 (SSC)
[    0.945021] brcm-pcie fd500000.pcie: PCI host bridge to bus 0000:00
[    0.945034] pci_bus 0000:00: root bus resource [bus 00-ff]
[    0.945048] pci_bus 0000:00: root bus resource [mem 0x600000000-0x603ffffff] (bus address [0xf8000000-0xfbffffff])
[    0.945091] pci 0000:00:00.0: [14e4:2711] type 01 class 0x060400
[    0.945279] pci 0000:00:00.0: PME# supported from D0 D3hot
[    0.948837] pci 0000:01:00.0: [1b21:1242] type 00 class 0x0c0330
[    0.948911] pci 0000:01:00.0: reg 0x10: [mem 0x00000000-0x00007fff 64bit]
[    0.949001] pci 0000:01:00.0: enabling Extended Tags
[    0.949179] pci 0000:01:00.0: PME# supported from D3hot D3cold
[    0.949280] pci 0000:01:00.0: 4.000 Gb/s available PCIe bandwidth, limited by 5 GT/s x1 link at 0000:00:00.0 (capable of 15.752 Gb/s with 8 GT/s x2 link)
[    0.961784] pci 0000:00:00.0: BAR 14: assigned [mem 0x600000000-0x6000fffff]
[    0.961802] pci 0000:01:00.0: BAR 0: assigned [mem 0x600000000-0x600007fff 64bit]
[    0.961831] pci 0000:00:00.0: PCI bridge to [bus 01]
[    0.961846] pci 0000:00:00.0:   bridge window [mem 0x600000000-0x6000fffff]
[    0.962100] pcieport 0000:00:00.0: enabling device (0000 -> 0002)
[    0.962289] pcieport 0000:00:00.0: PME: Signaling with IRQ 43
[    0.962633] pcieport 0000:00:00.0: AER: enabled with IRQ 43
[    0.962891] pci 0000:01:00.0: enabling device (0000 -> 0002)
[    0.963297] bcm2708_fb soc:fb: Unable to determine number of FBs. Disabling driver.
[    0.963333] bcm2708_fb: probe of soc:fb failed with error -2
[    0.965159] raspberrypi-clk firmware-clocks: CPU frequency range: min 600000000, max 1500000000
[    1.024582] Serial: 8250/16550 driver, 1 ports, IRQ sharing enabled
[    1.026745] iproc-rng200 fe104000.rng: hwrng registered
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

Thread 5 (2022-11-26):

PX4 firmware hex / binary file

hwjalapeno, 2022-11-26:
Hi,
I am trying to design a new version of Pixhawk-based board (for which I am thinking of using your baseboard design) for a project, to add jetson nano instead of raspberry pi, and in my design, I am not sure how you have managed to to provide direct bootloader access to only the pixhawk, so have you already compiled a hex or binary for just PX4, so that atleast I can upload it on JTAG, thanks!

CRVARUN, 2022-12-01:
Follow-up question, do I have to download a bootloader specific to H7 MCU, and how did you guys compile it? It would be great if we could collaborate on this project together

Closed 2022-12-26.

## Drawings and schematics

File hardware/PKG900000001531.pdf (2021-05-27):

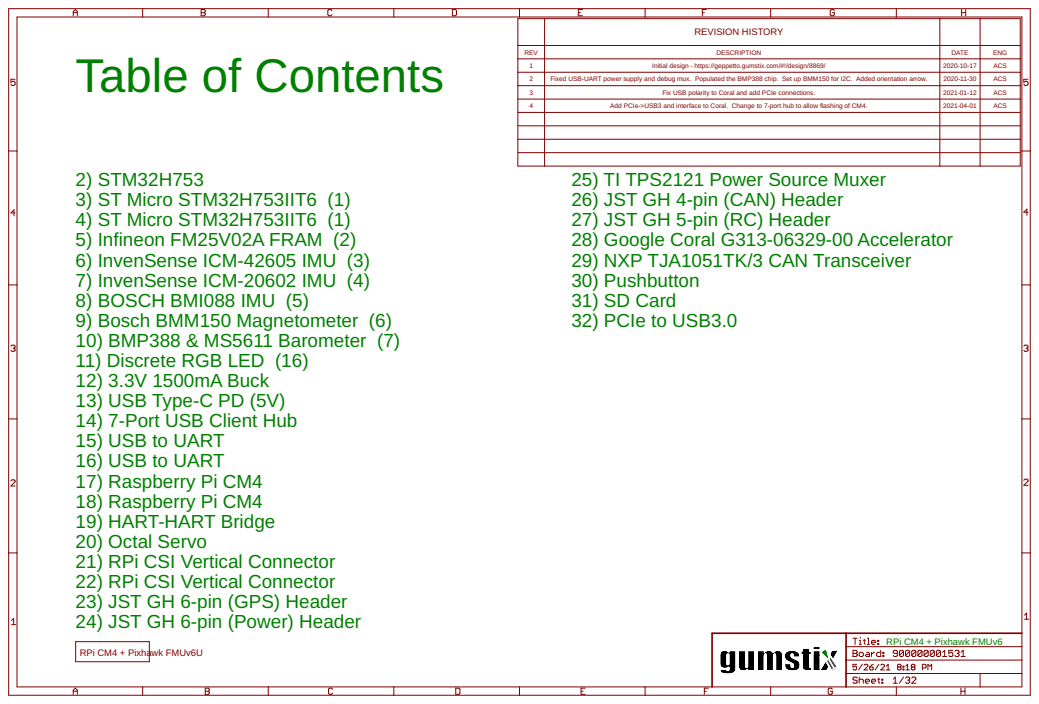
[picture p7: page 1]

REV 1 | DESCRIPTION Initial design - https://geppetto.gumstix.com/#!/design/8869/ | DATE 2020-10-17 | ENG Table of Contents ACS

2 | Fixed USB-UART power supply and debug mux. Populated the BMP388 chip. Set up BMM150 for I2C. Added orientation arrow. | 2020-11-30 | ACS
3 | Fix USB polarity to Coral and add PCIe connections. | 2021-01-12 | ACS
4 | Add PCIe->USB3 and interface to Coral. Change to 7-port hub to allow flashing of CM4. | 2021-04-01 | ACS

2) STM32H753
3) ST Micro STM32H753IIT6 (1)
4) ST Micro STM32H753IIT6 (1)
5) Infineon FM25V02A FRAM (2)
6) InvenSense ICM-42605 IMU (3)
7) InvenSense ICM-20602 IMU (4)
8) BOSCH BMI088 IMU (5)
9) Bosch BMM150 Magnetometer (6)
10) BMP388 & MS5611 Barometer (7)
11) Discrete RGB LED (16)
12) 3.3V 1500mA Buck
13) USB Type-C PD (5V)
14) 7-Port USB Client Hub
15) USB to UART
16) USB to UART
17) Raspberry Pi CM4
18) Raspberry Pi CM4
19) HART-HART Bridge
20) Octal Servo
21) RPi CSI Vertical Connector
22) RPi CSI Vertical Connector
23) JST GH 6-pin (GPS) Header
24) JST GH 6-pin (Power) Header

25) TI TPS2121 Power Source Muxer
26) JST GH 4-pin (CAN) Header
27) JST GH 5-pin (RC) Header
28) Google Coral G313-06329-00 Accelerator
29) NXP TJA1051TK/3 CAN Transceiver
30) Pushbutton
31) SD Card
32) PCIe to USB3.0

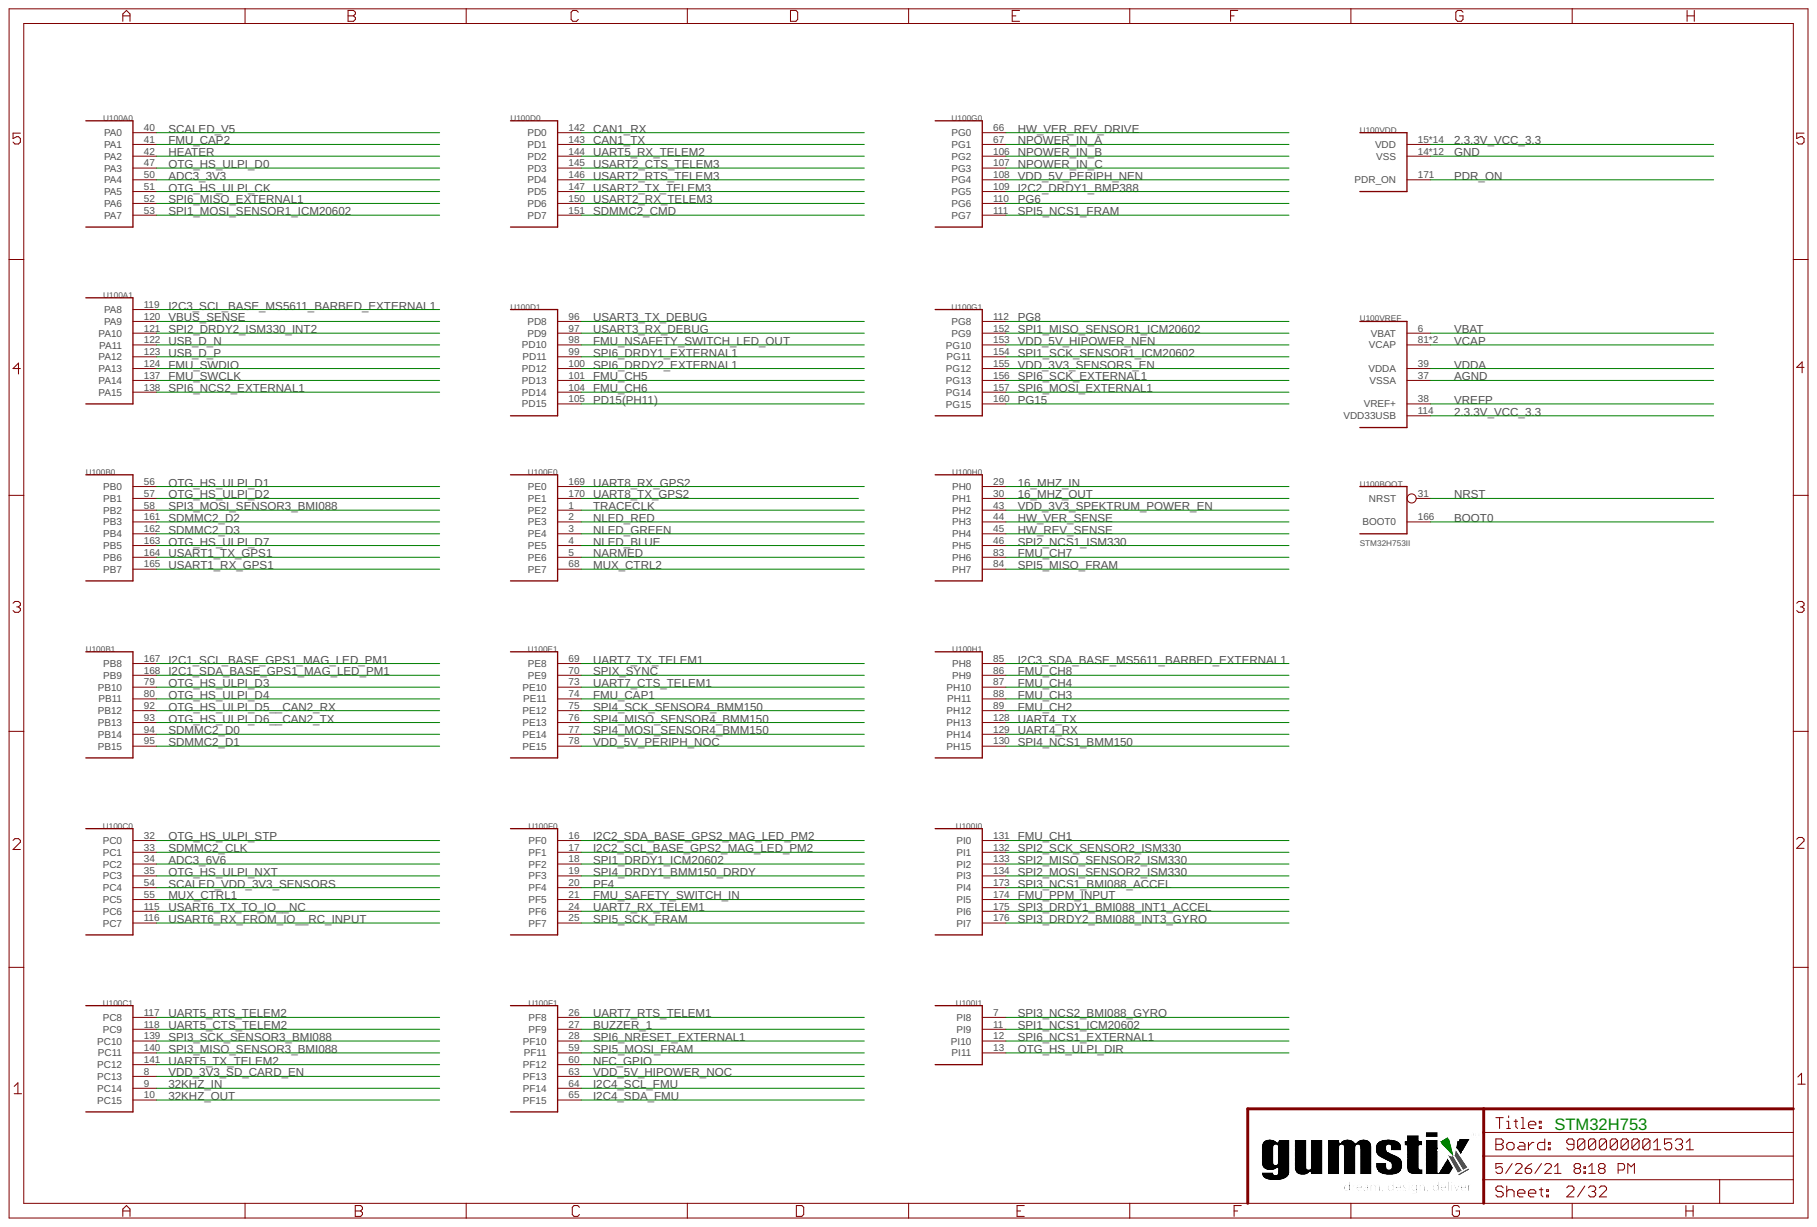
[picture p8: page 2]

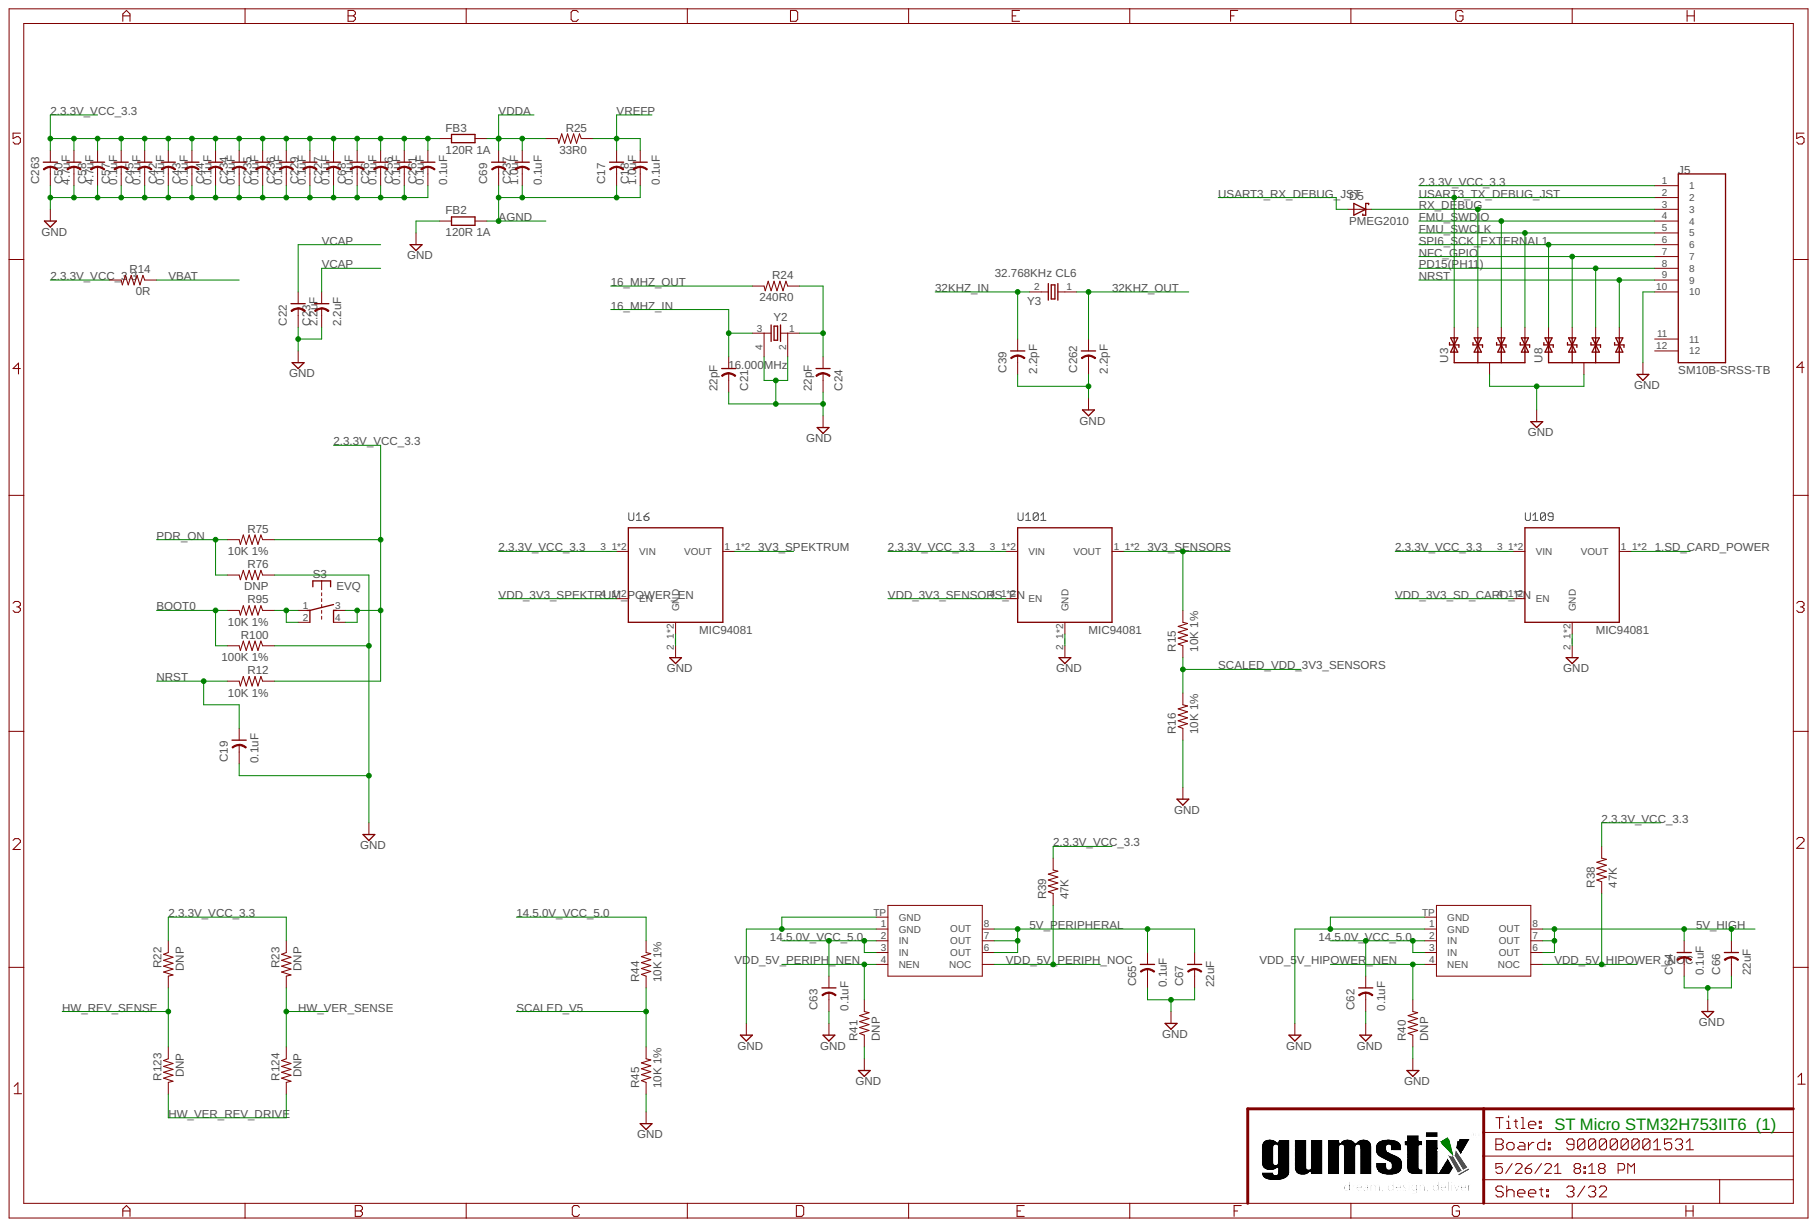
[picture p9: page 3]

SM10B-SRSS-TB GND GND

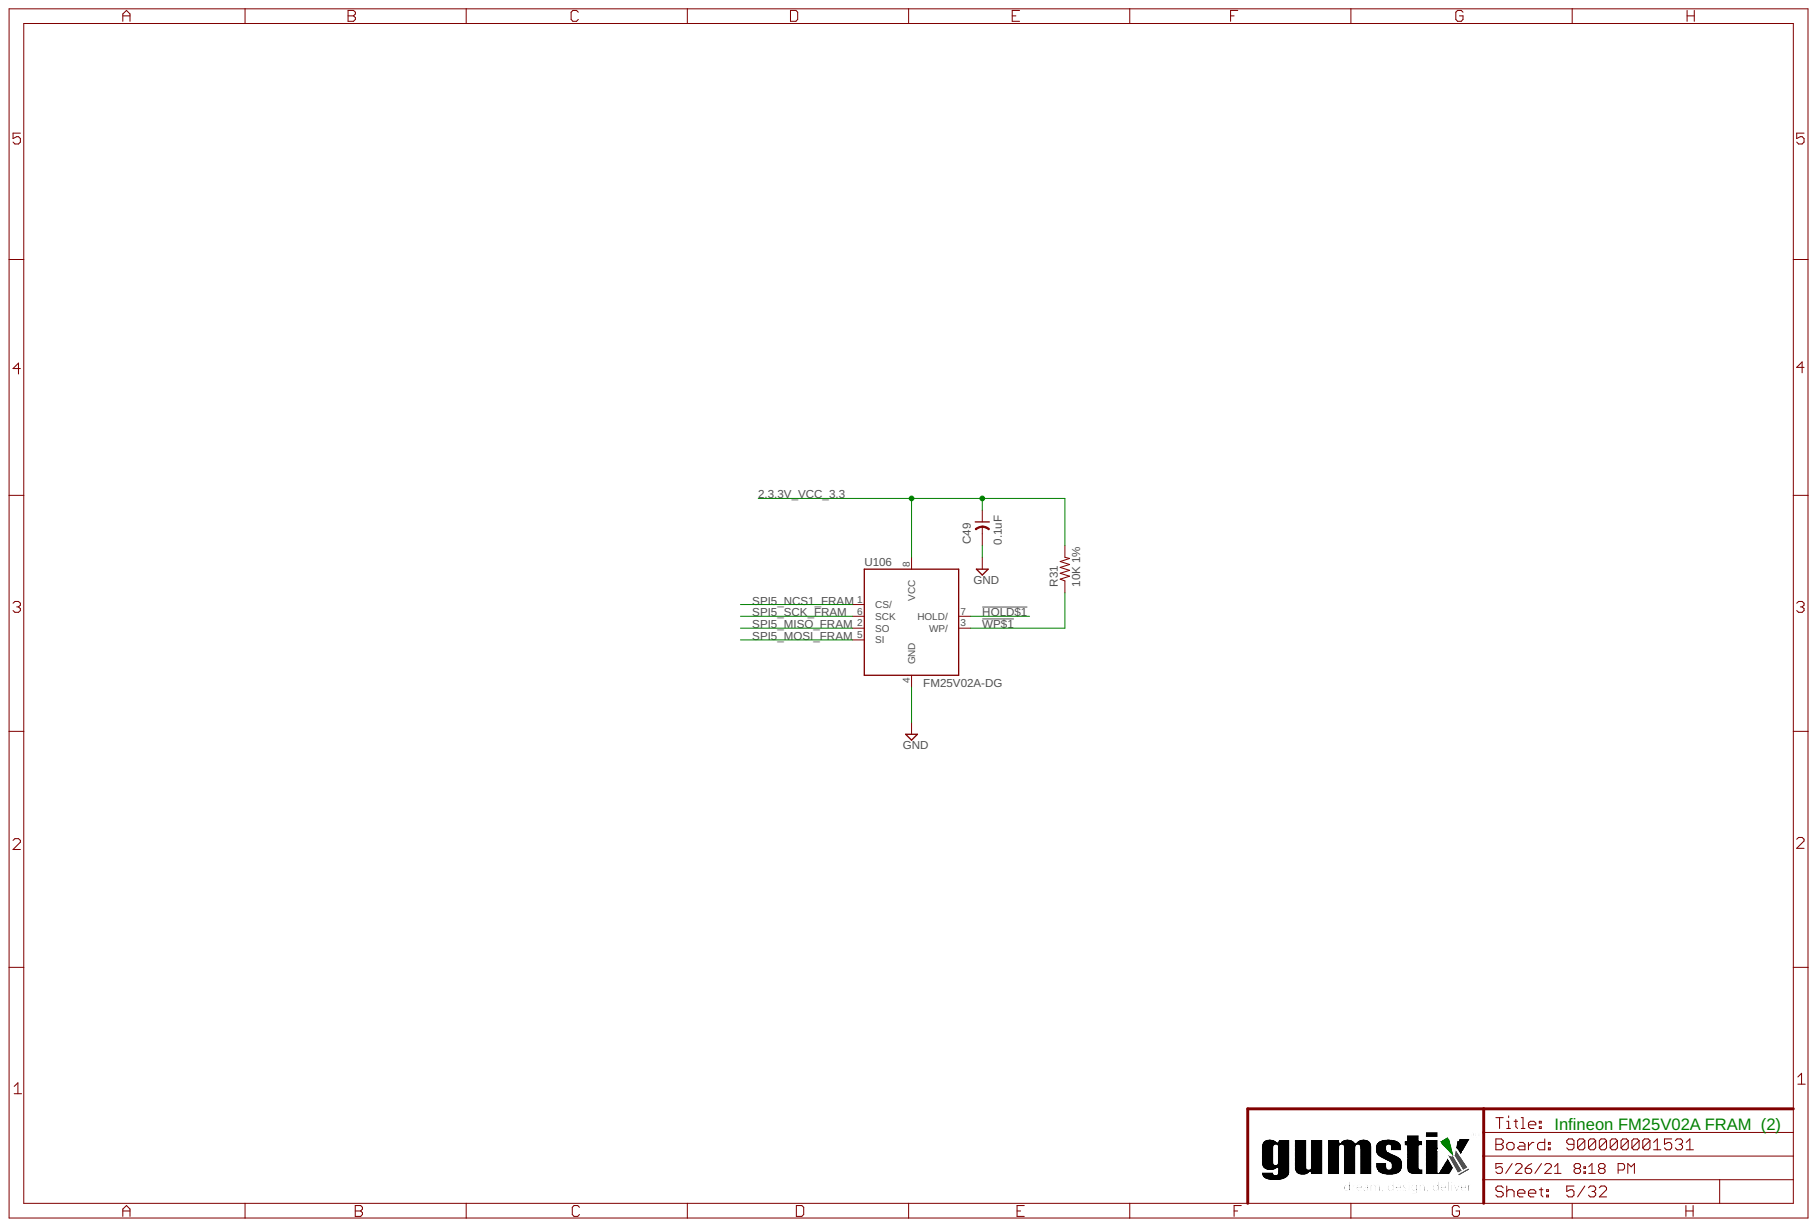
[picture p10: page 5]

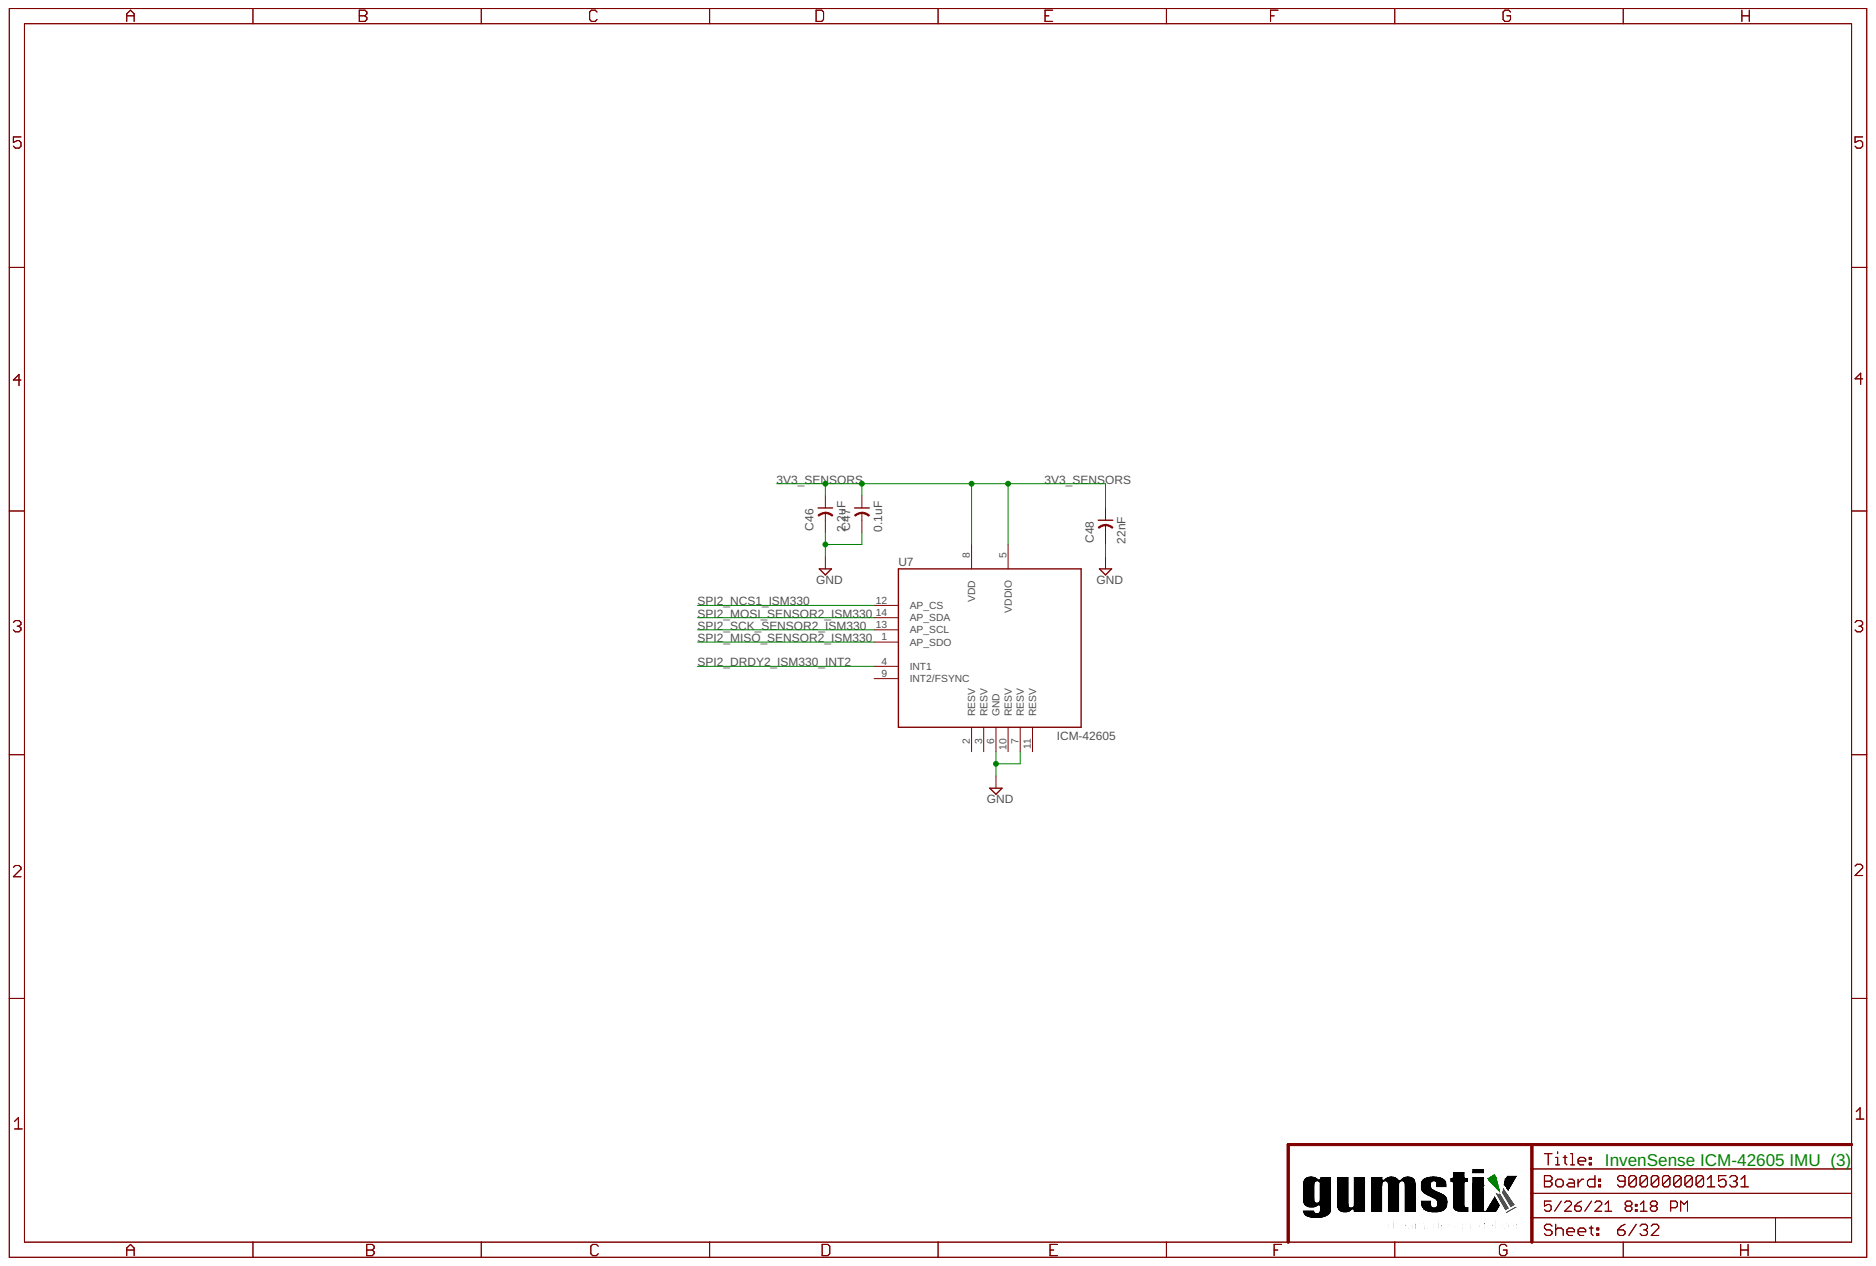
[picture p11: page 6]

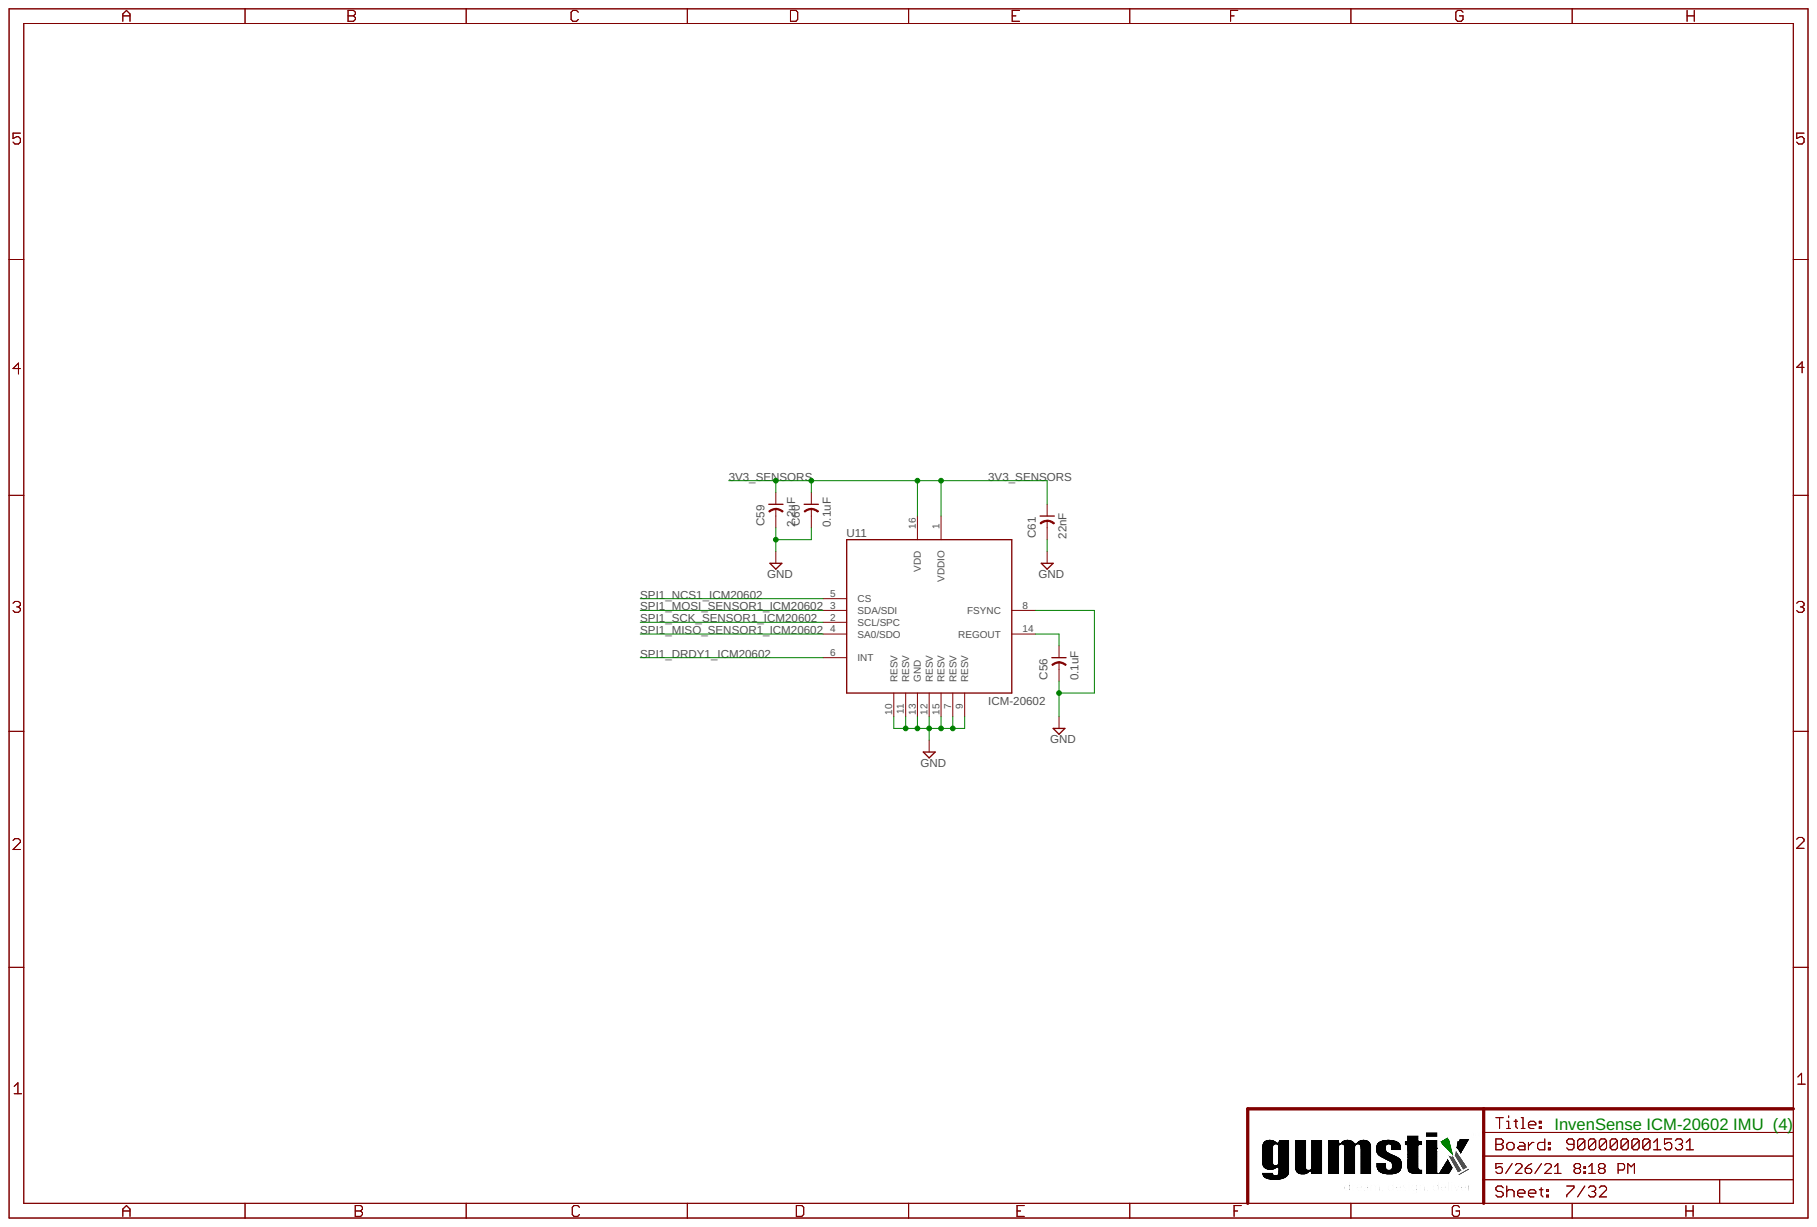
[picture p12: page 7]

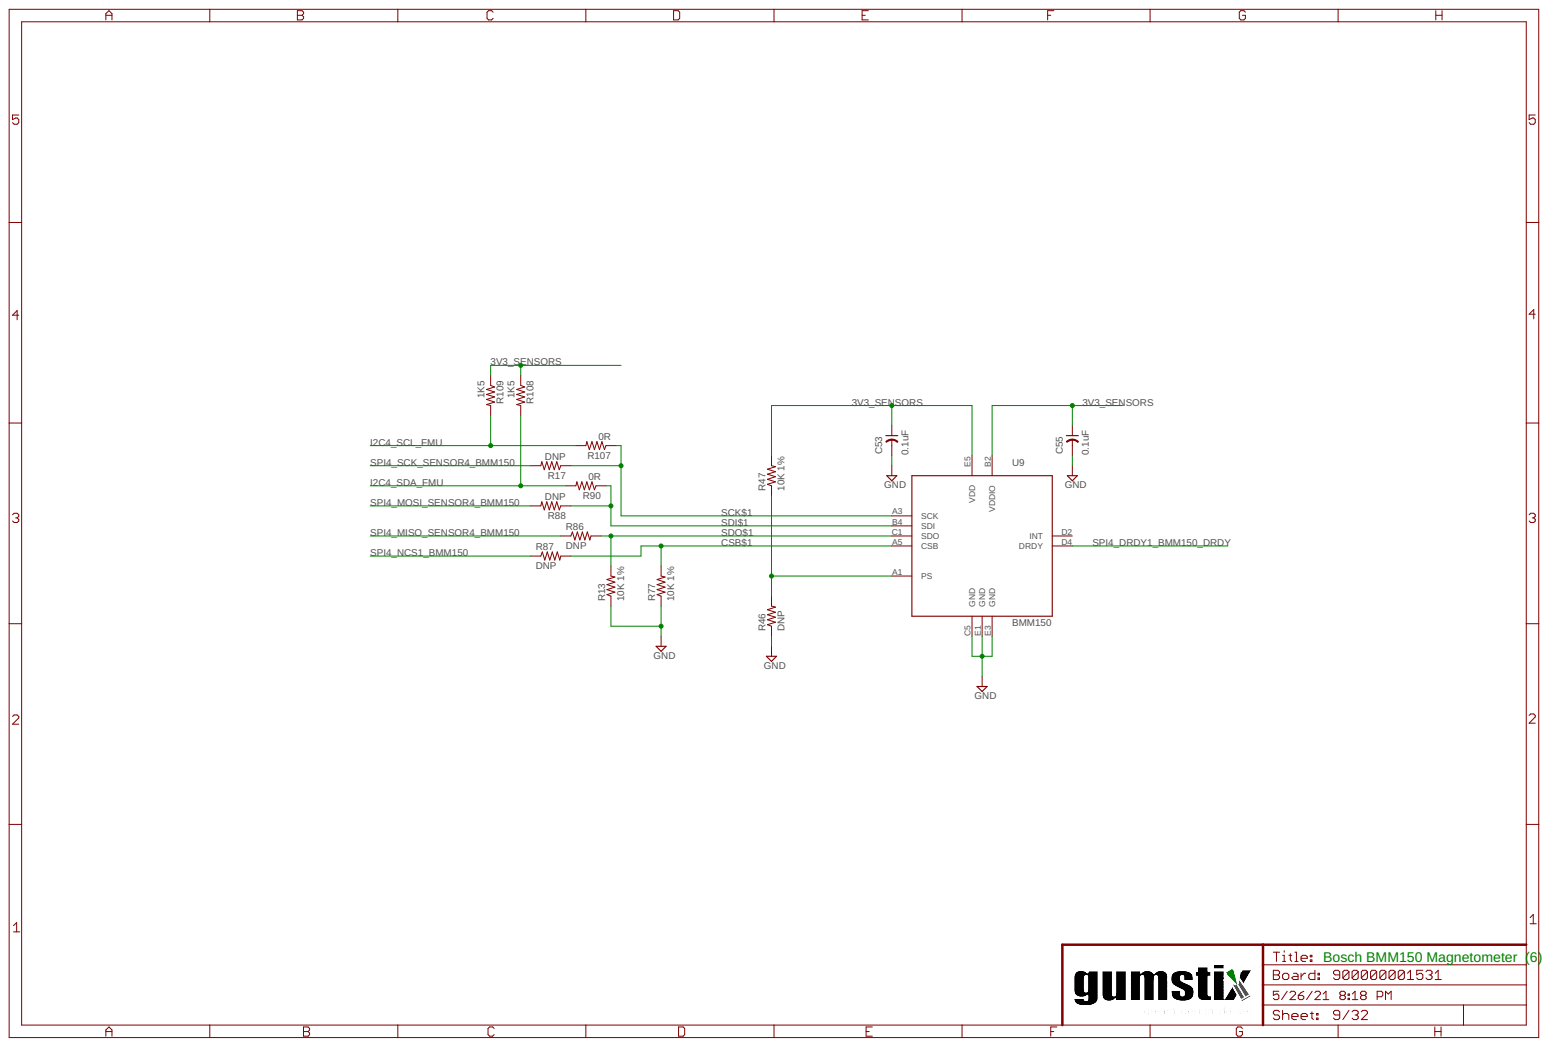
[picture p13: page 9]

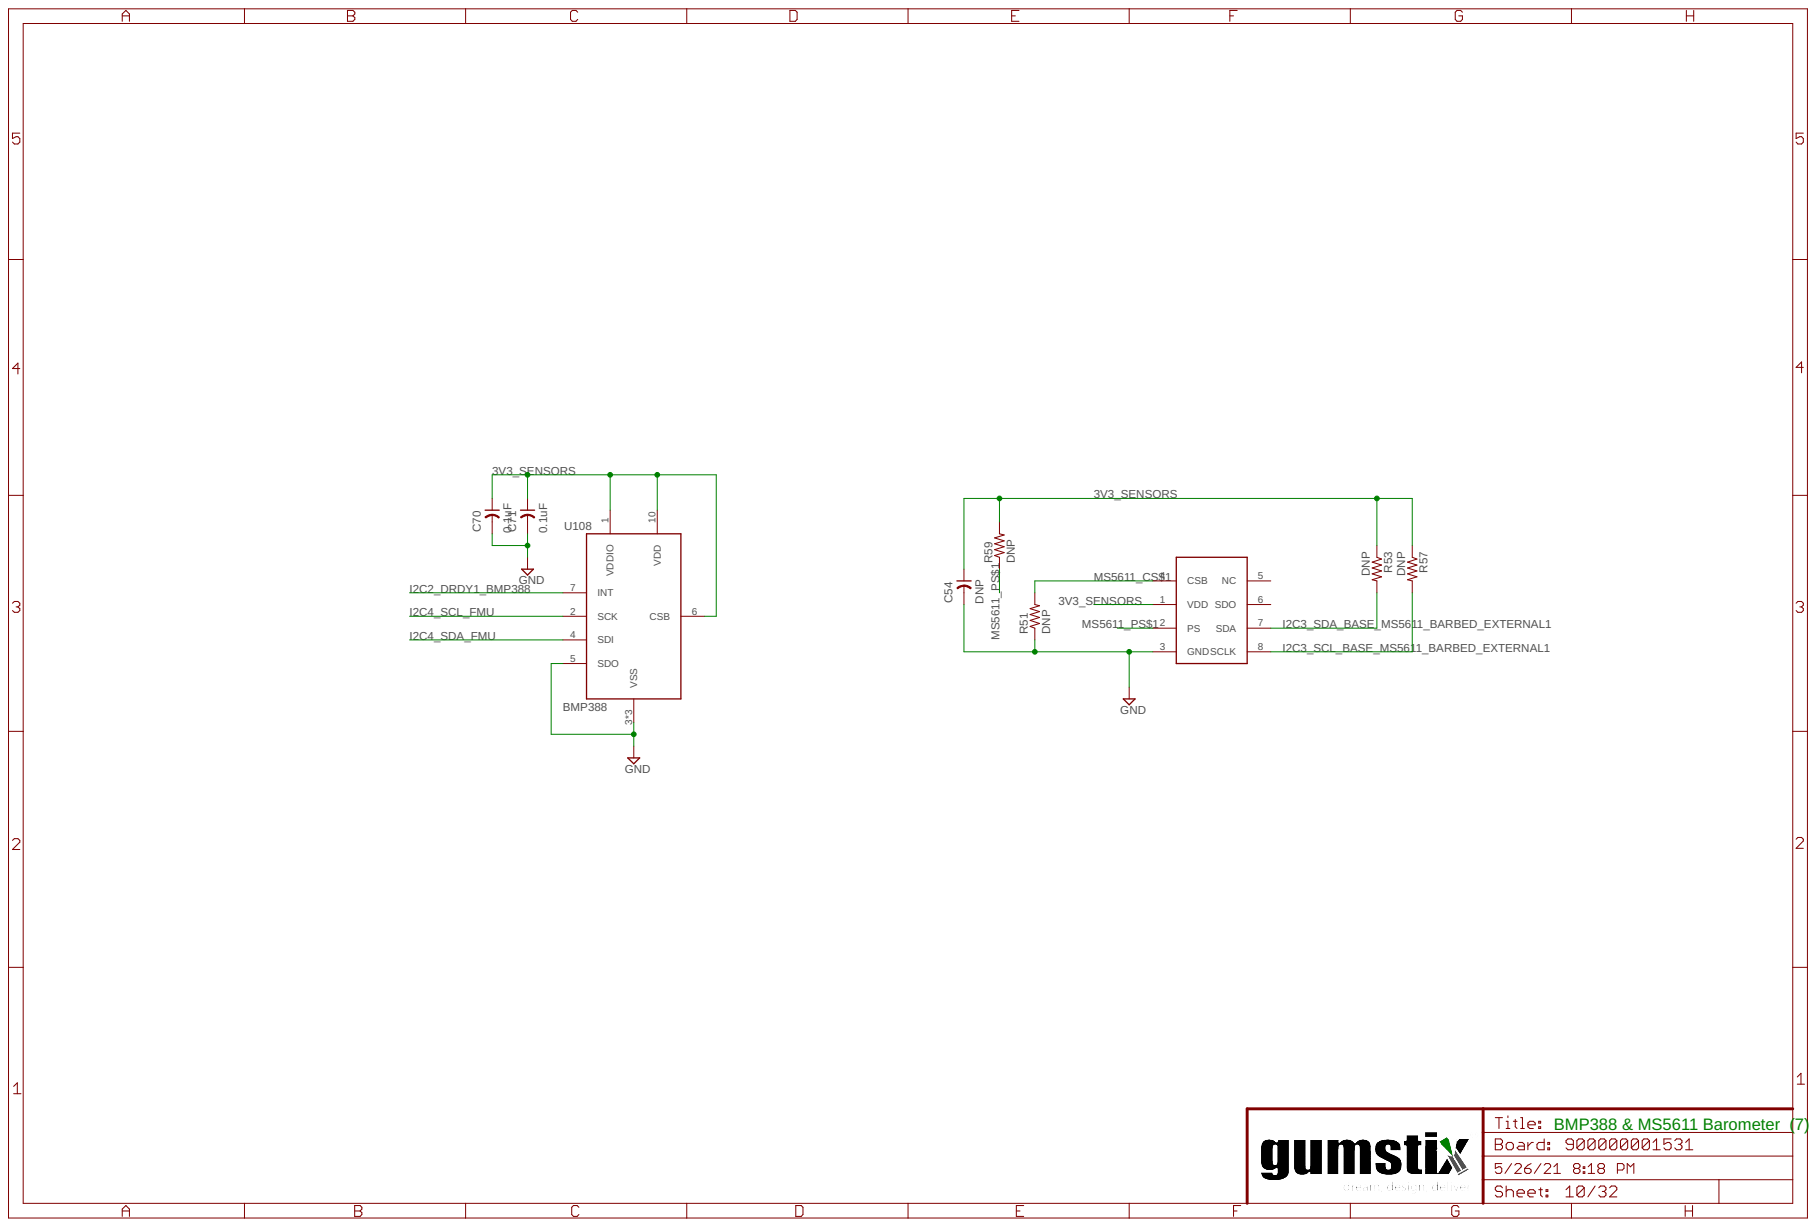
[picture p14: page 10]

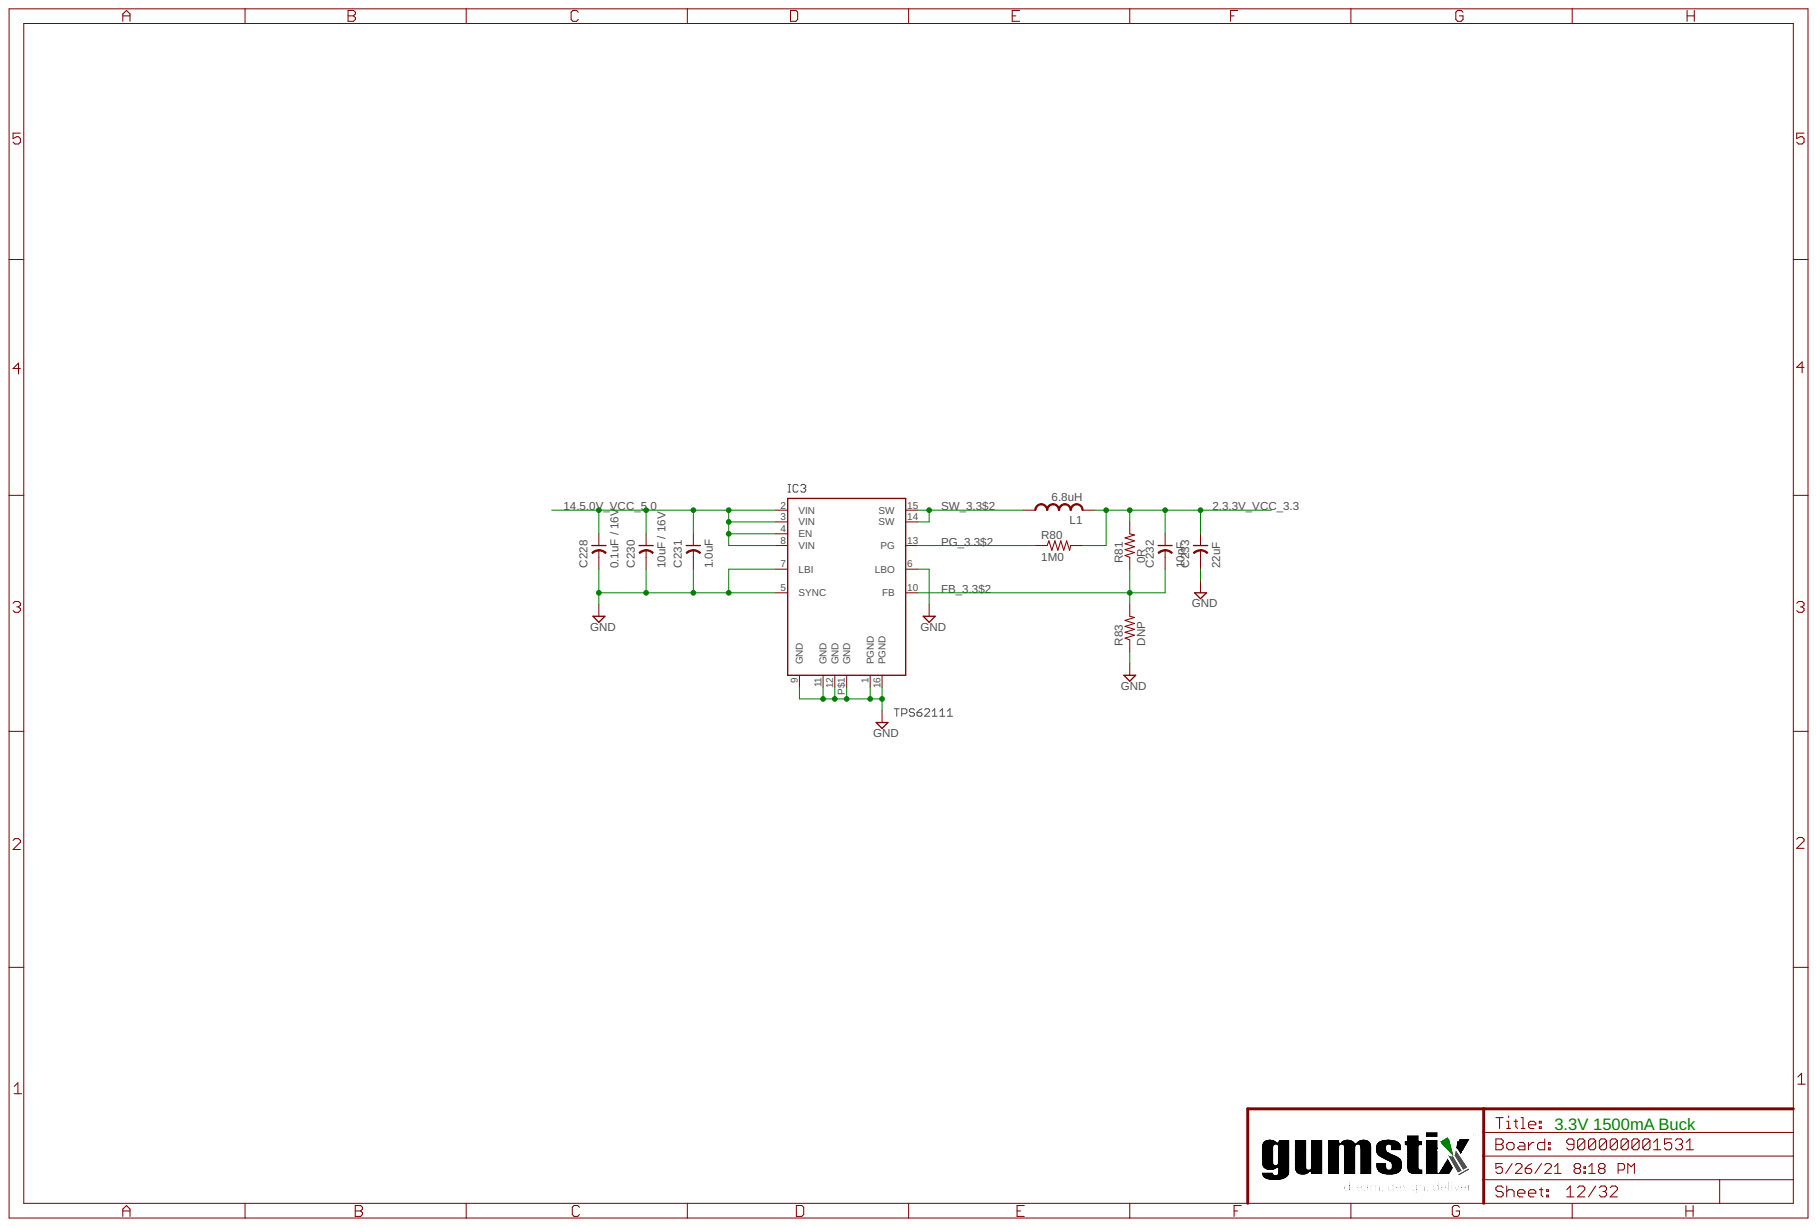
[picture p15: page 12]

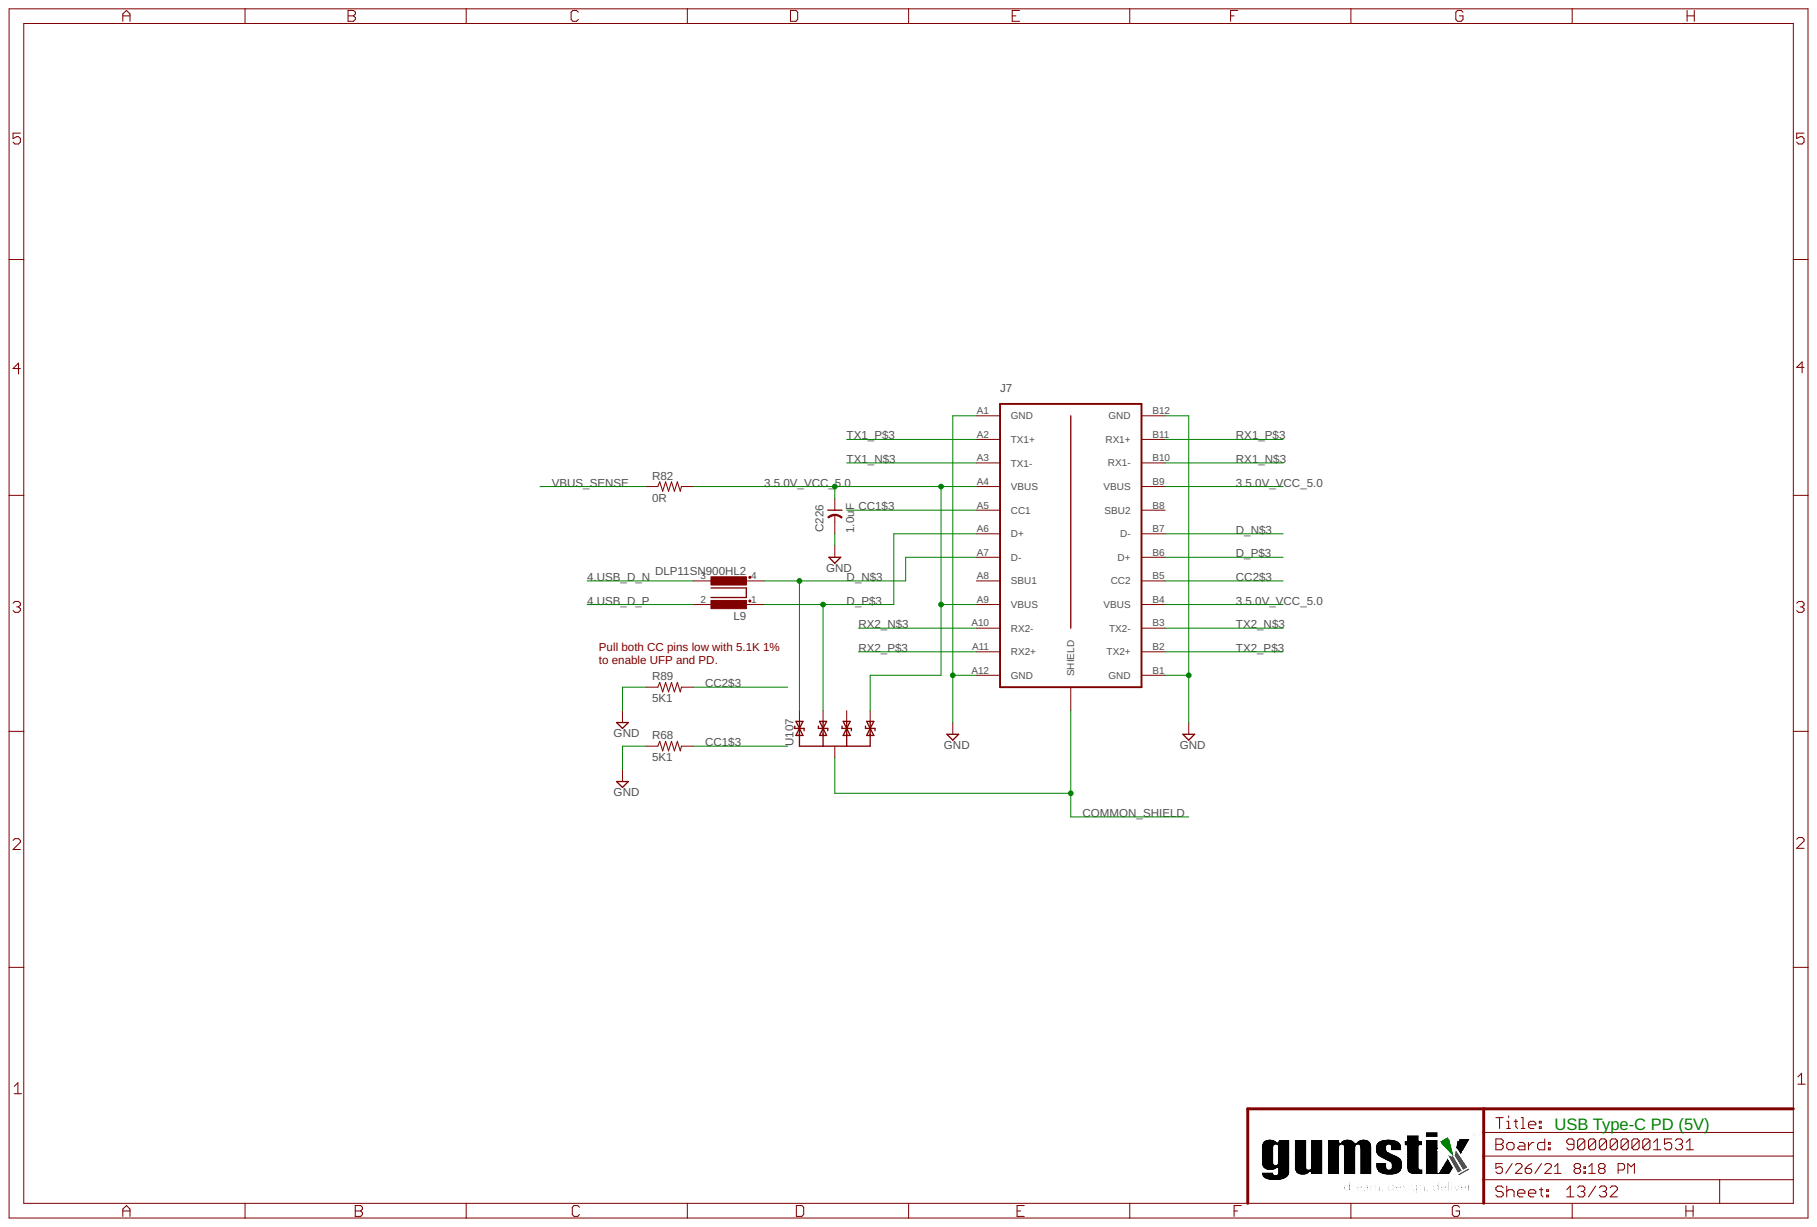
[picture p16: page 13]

Pull both CC pins low with 5.1K 1%
to enable UFP and PD.

7-Port USB Client Hub

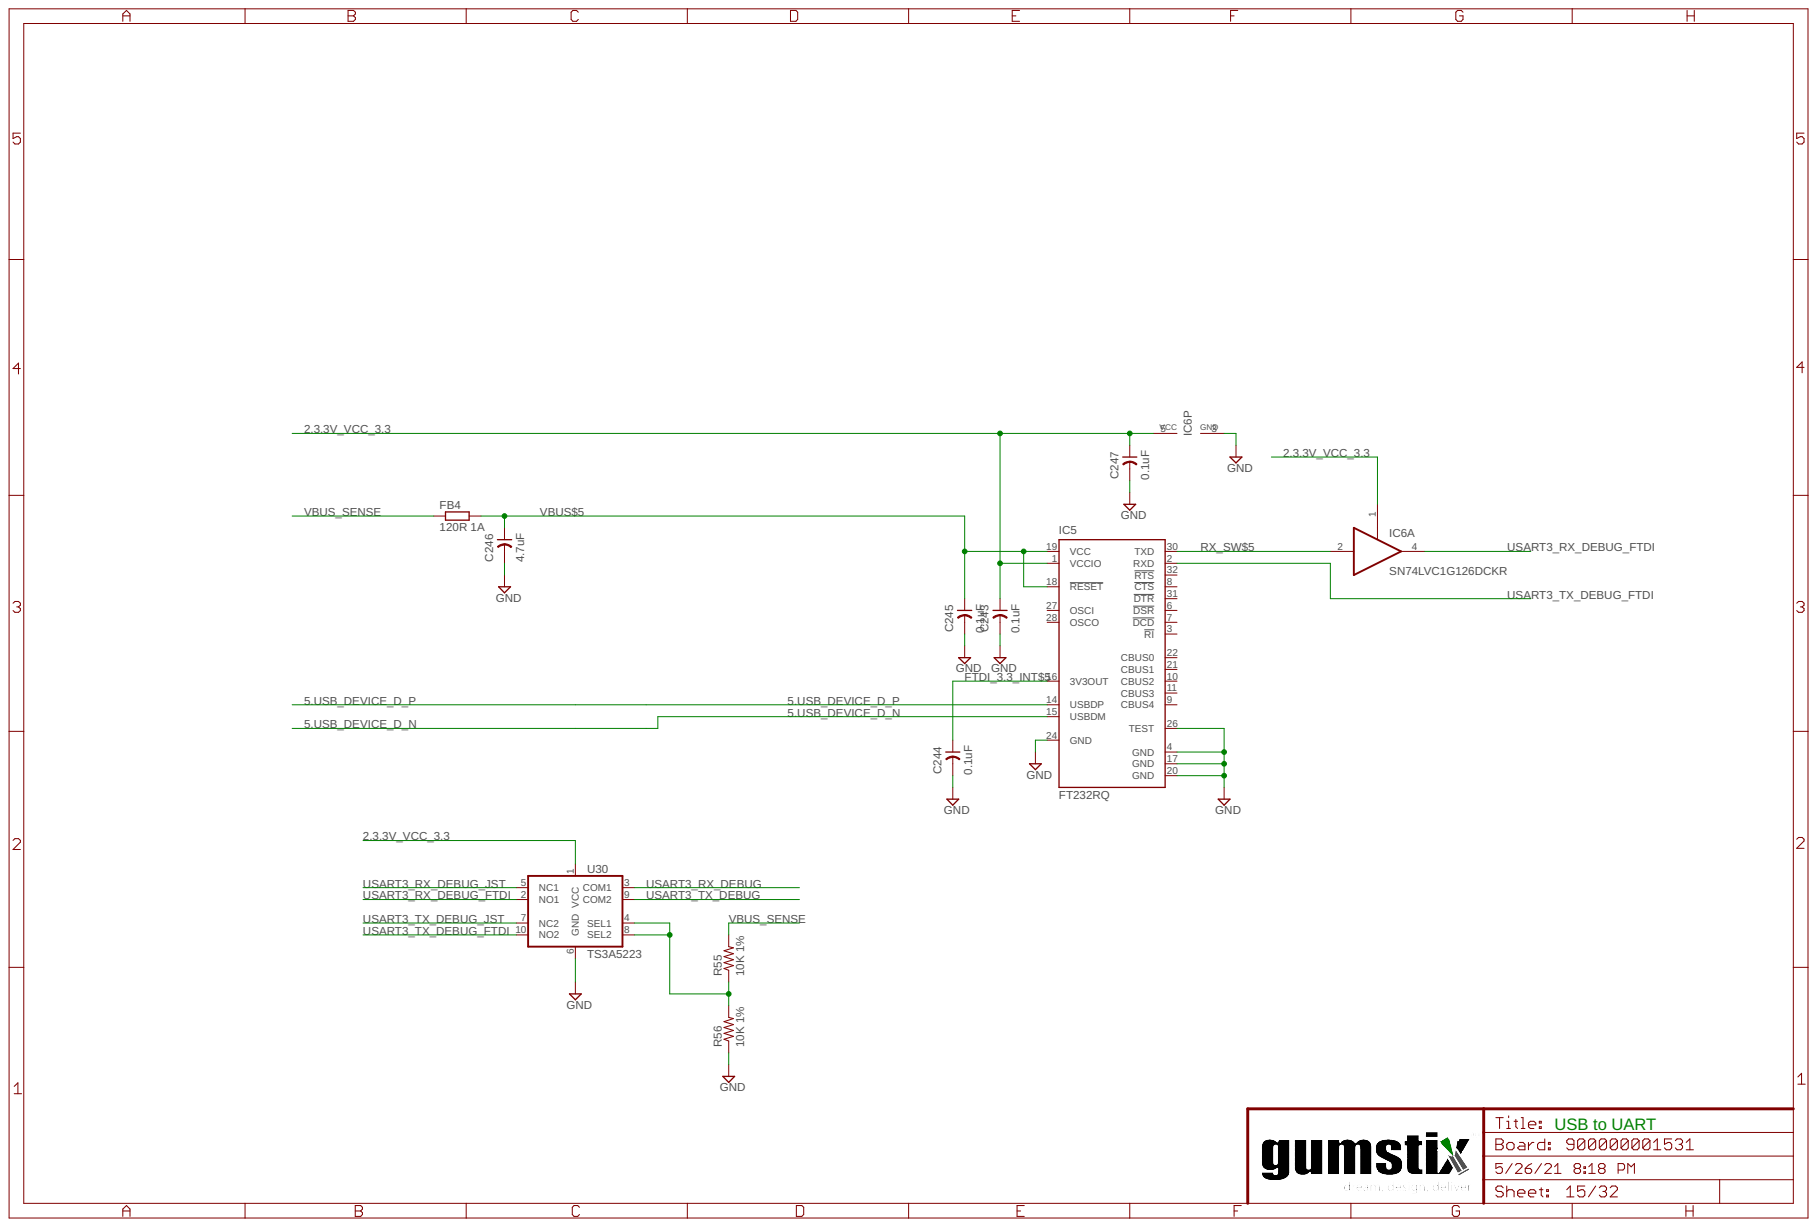
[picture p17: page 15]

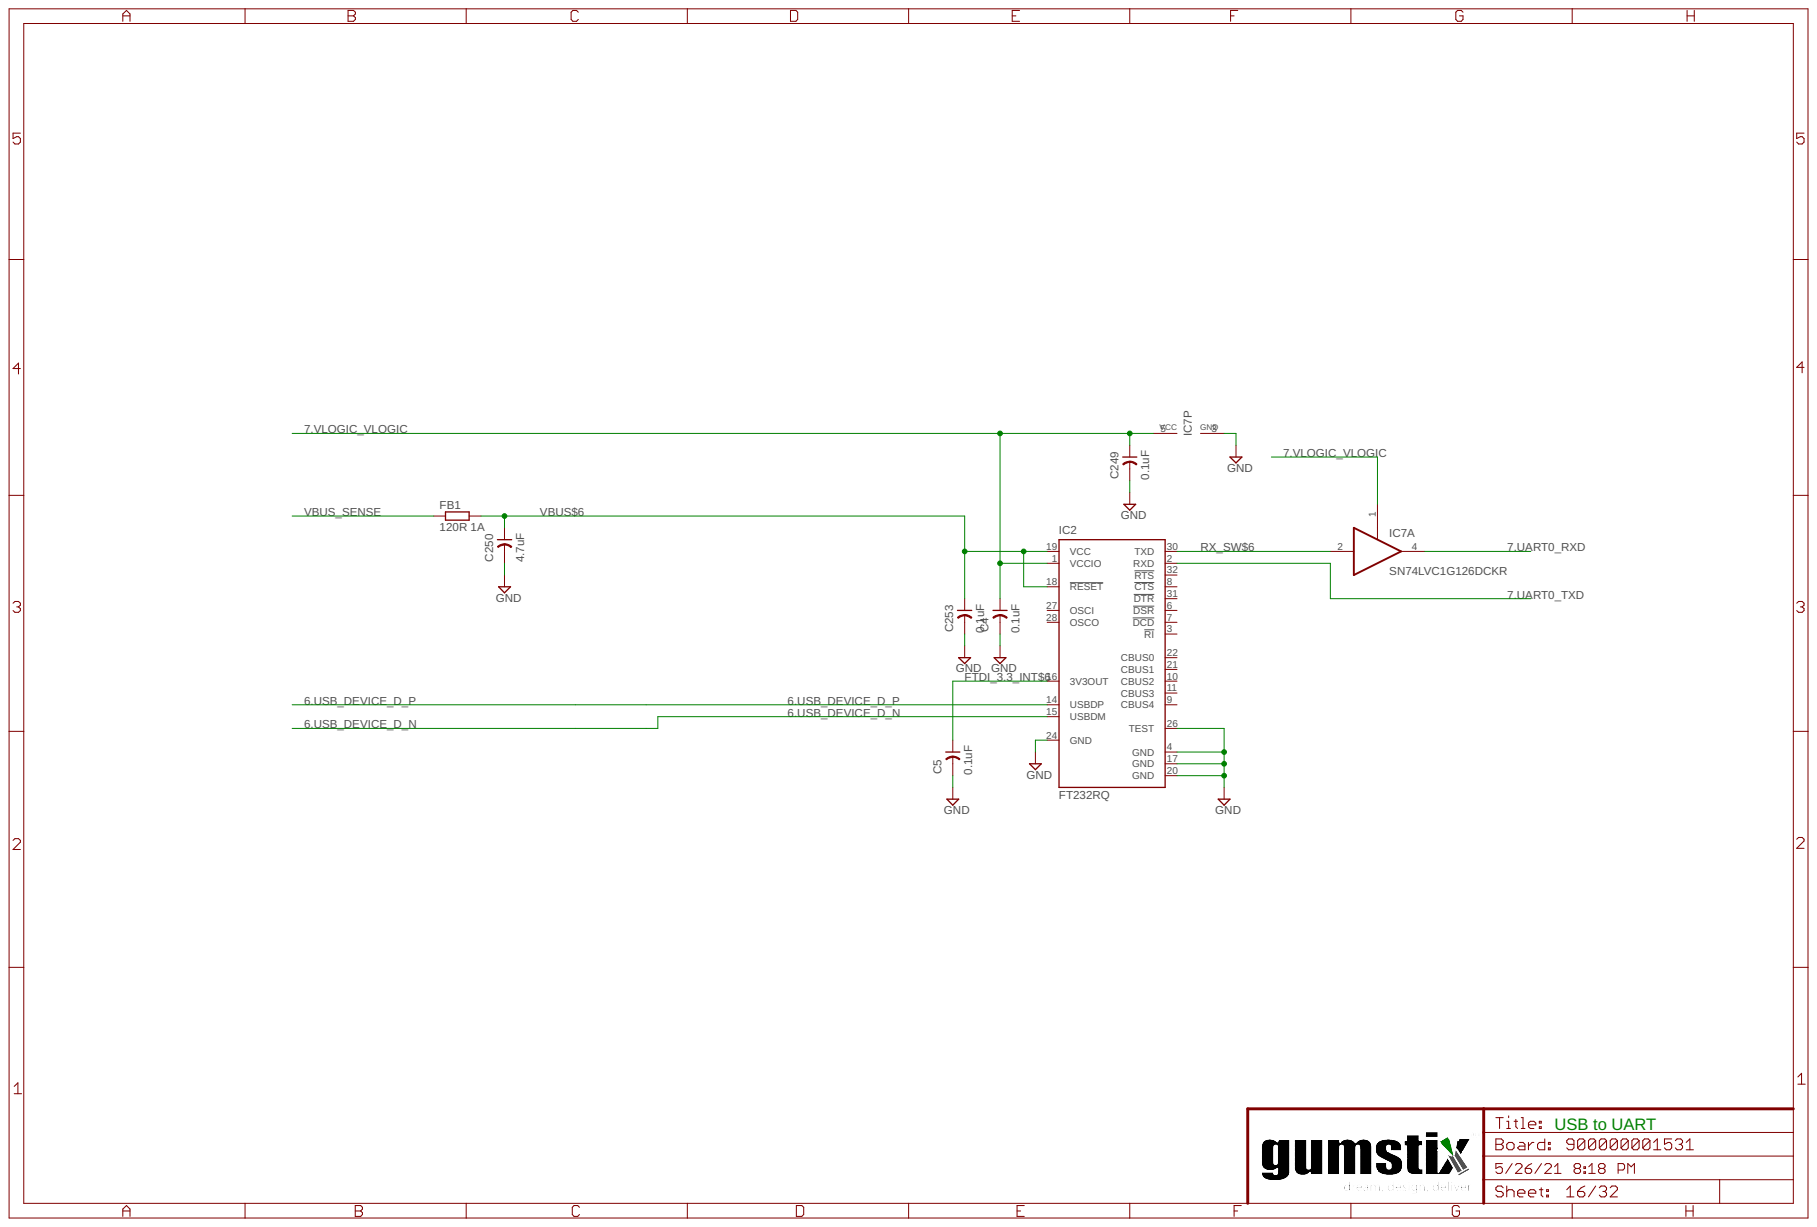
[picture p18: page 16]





RPi CSI Vertical Connector


RPi CSI Vertical Connector


JST GH 6-pin (GPS) Header

JST GH 6-pin (Power) Header


TI TPS2121 Power Source Muxer


JST GH 4-pin (CAN) Header

JST GH 5-pin (RC) Header





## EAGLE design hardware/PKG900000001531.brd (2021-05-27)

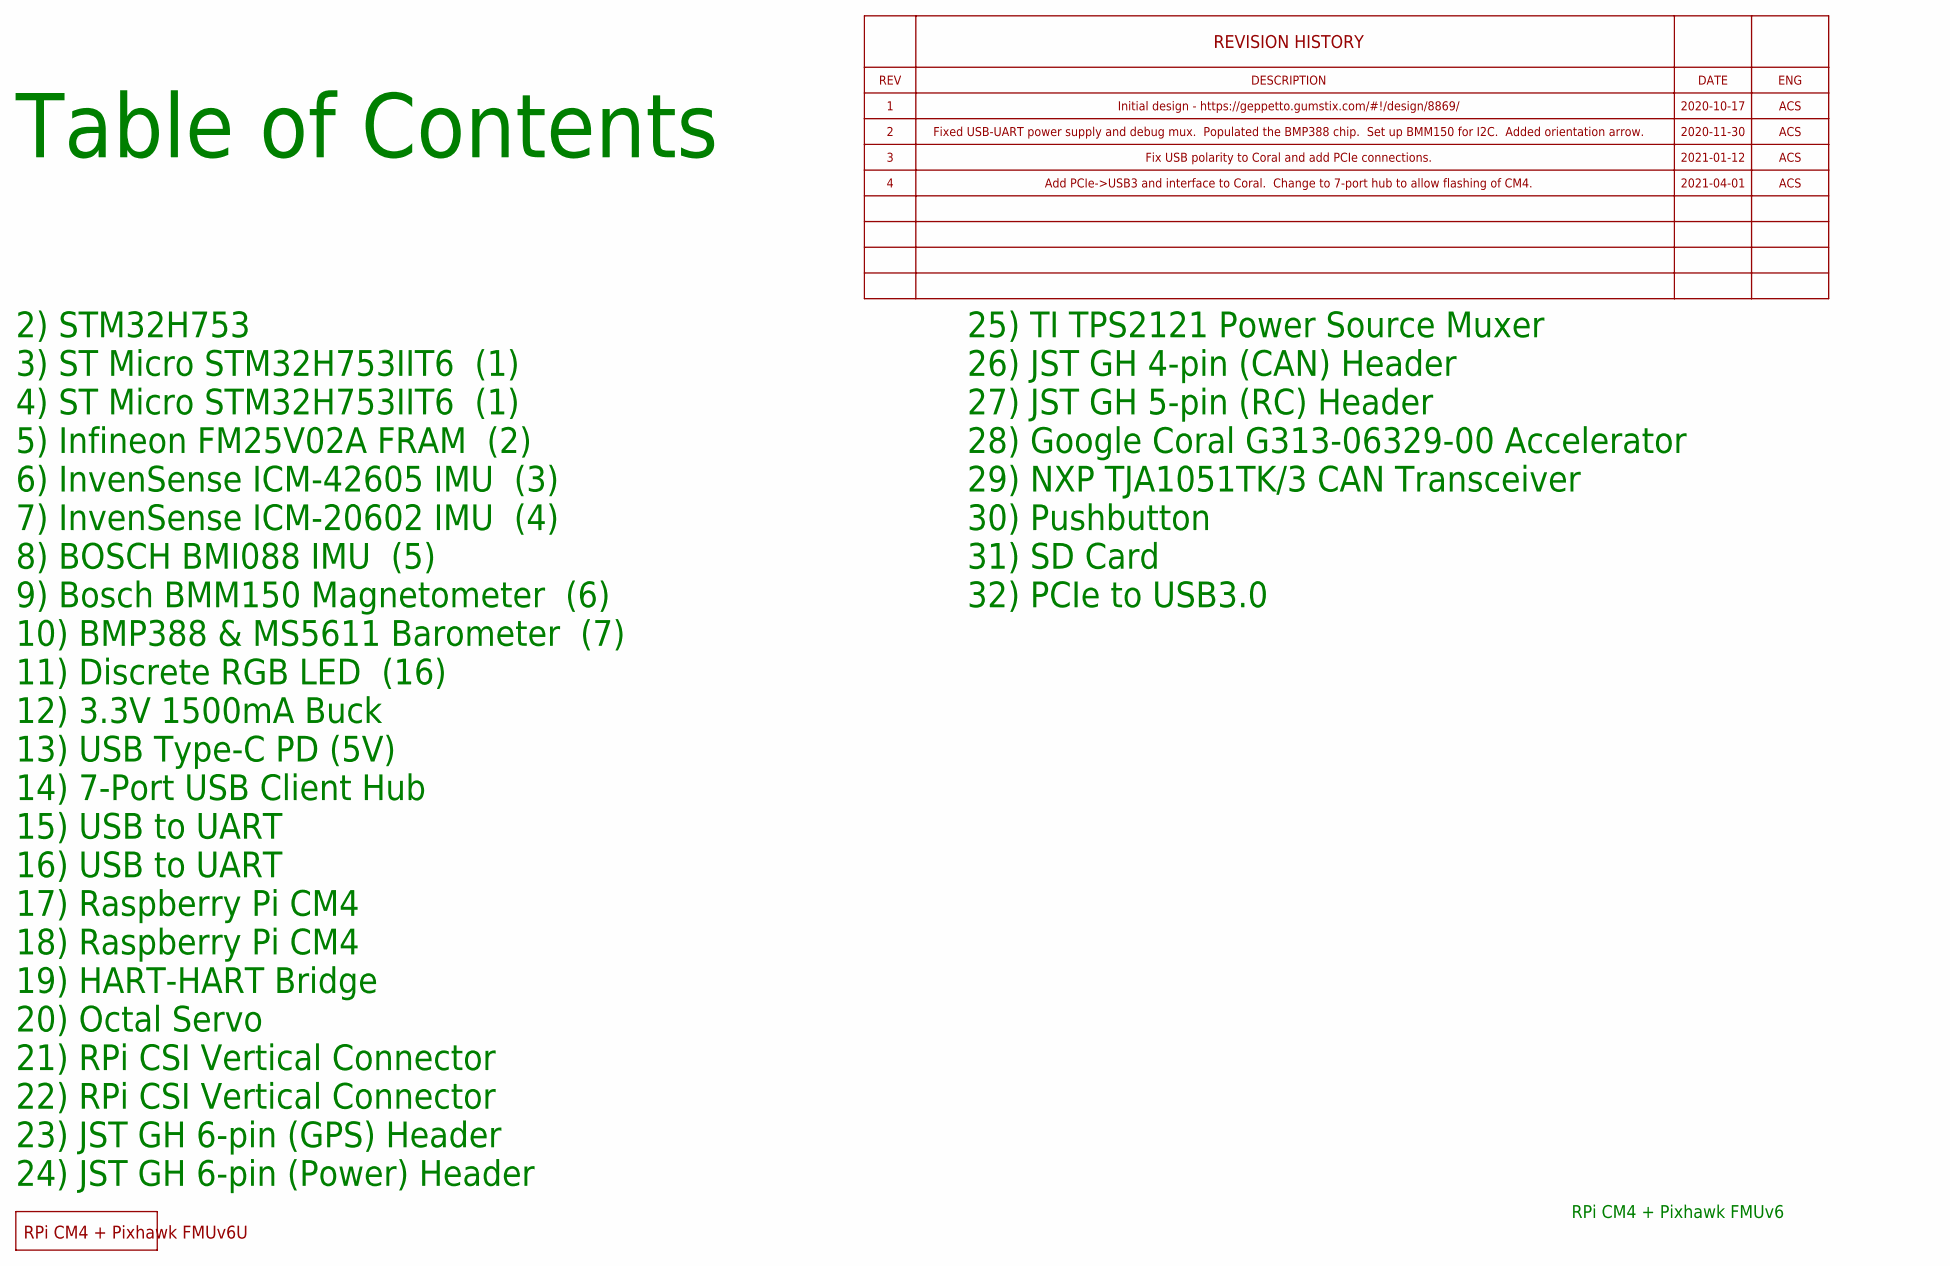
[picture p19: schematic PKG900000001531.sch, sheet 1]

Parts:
FD1, FD2, FD3, FD4, FD5, FD6, FD7, FD8: DNP; FIDUCIAL
U$2: DNP; UPVERTER_LABEL_SMALL

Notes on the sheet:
Table of Contents
RPi CM4 + Pixhawk FMUv6
2) STM32H753
3) ST Micro STM32H753IIT6 (1)
4) ST Micro STM32H753IIT6 (1)
5) Infineon FM25V02A FRAM (2)
6) InvenSense ICM-42605 IMU (3)
7) InvenSense ICM-20602 IMU (4)
8) BOSCH BMI088 IMU (5)
9) Bosch BMM150 Magnetometer (6)
10) BMP388 & MS5611 Barometer (7)
11) Discrete RGB LED (16)
12) 3.3V 1500mA Buck
13) USB Type-C PD (5V)
14) 7-Port USB Client Hub
15) USB to UART
16) USB to UART
17) Raspberry Pi CM4
18) Raspberry Pi CM4
19) HART-HART Bridge
20) Octal Servo
21) RPi CSI Vertical Connector
22) RPi CSI Vertical Connector
23) JST GH 6-pin (GPS) Header
24) JST GH 6-pin (Power) Header
25) TI TPS2121 Power Source Muxer
26) JST GH 4-pin (CAN) Header
27) JST GH 5-pin (RC) Header
28) Google Coral G313-06329-00 Accelerator
29) NXP TJA1051TK/3 CAN Transceiver
30) Pushbutton
31) SD Card
32) PCIe to USB3.0
Initial design - https://geppetto.gumstix.com/#\!/design/8869/
2020-10-17
ACS
2020-11-30
Fixed USB-UART power supply and debug mux. Populated the BMP388 chip. Set up BMM150 for I2C. Added orientation arrow.
Fix USB polarity to Coral and add PCIe connections.
2021-01-12

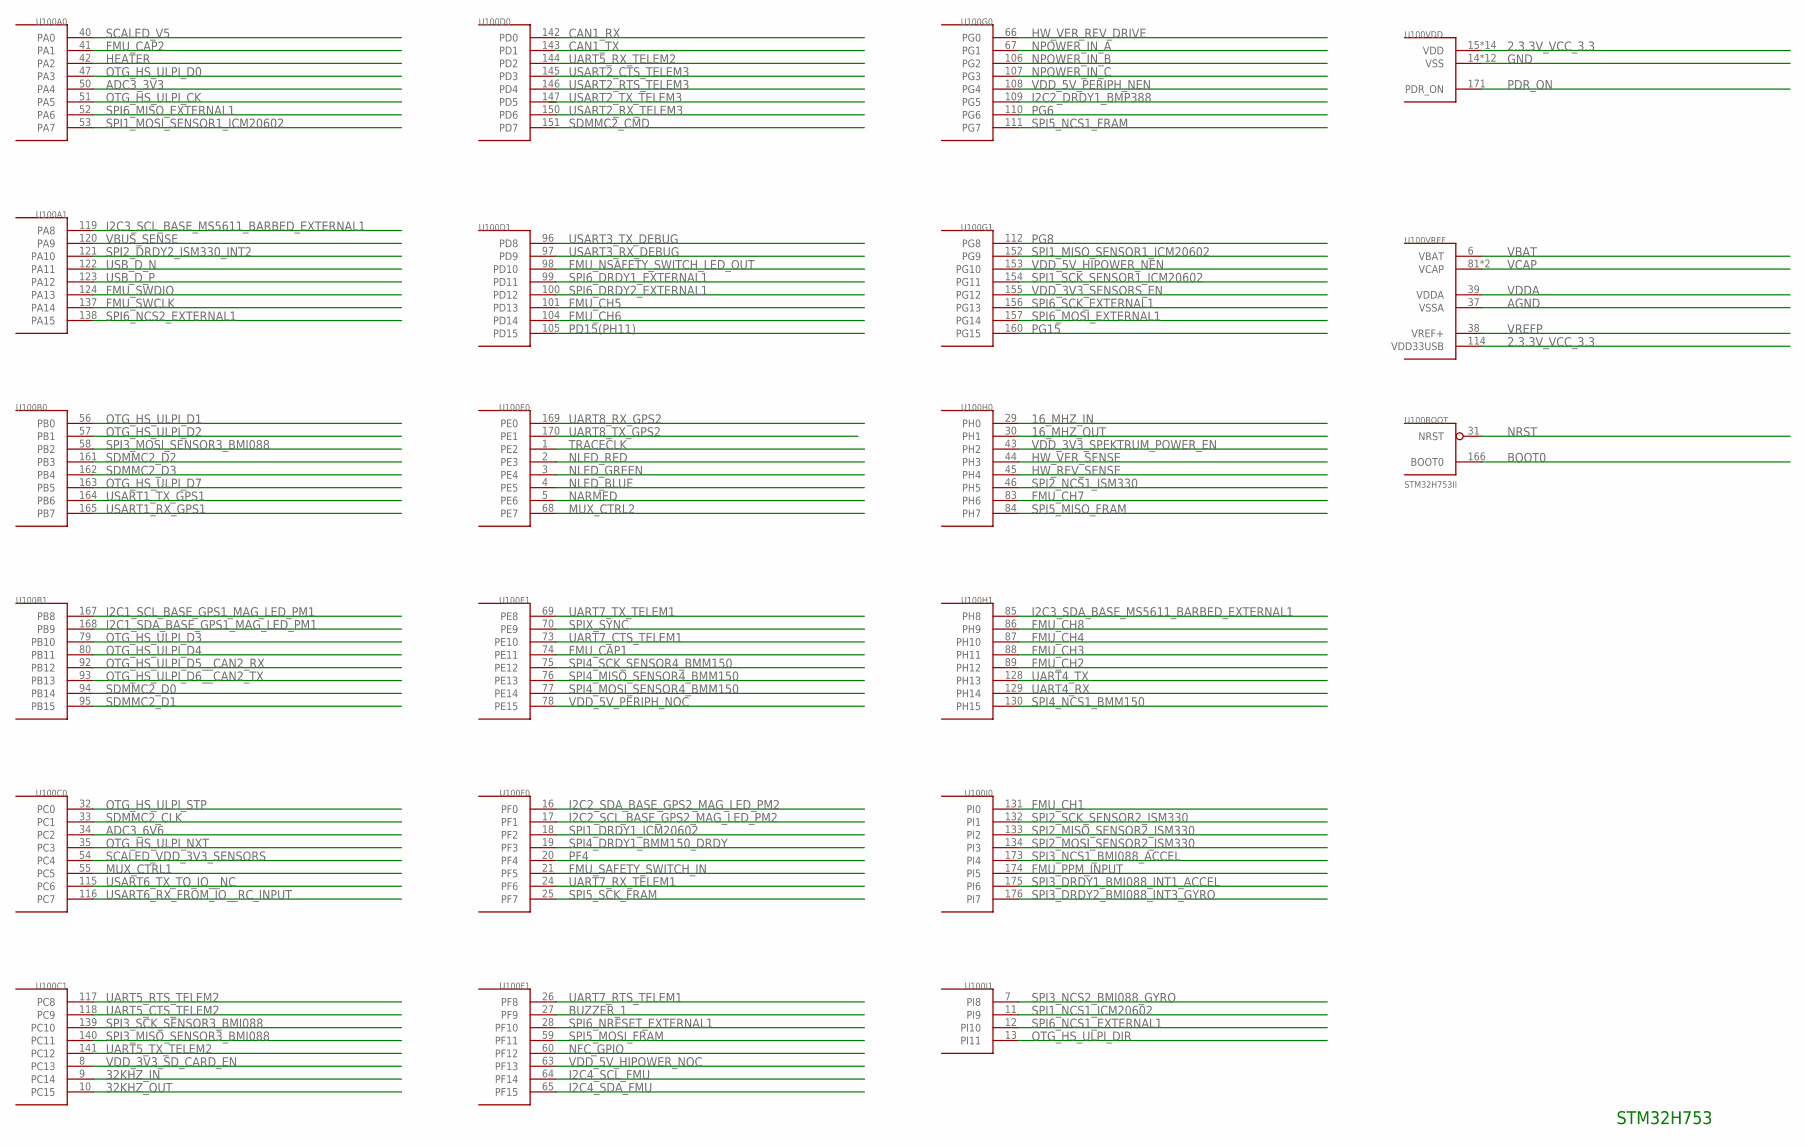
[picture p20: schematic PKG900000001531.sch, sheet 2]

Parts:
U100: STM32H753II; LQFP176

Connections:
2.3.3V_VCC_3.3: U100.15 (VDD), U100.23 (VDD), U100.36 (VDD), U100.49 (VDD), U100.62 (VDD), U100.72 (VDD), U100.82 (VDD), U100.91 (VDD), U100.103 (VDD), U100.114 (VDD33USB), U100.127 (VDD), U100.136 (VDD), U100.149 (VDD), U100.159 (VDD), U100.172 (VDD); also elsewhere on the board
16_MHZ_IN: U100.29 (PH0); also elsewhere on the board
16_MHZ_OUT: U100.30 (PH1); also elsewhere on the board
32KHZ_IN: U100.9 (PC14); also elsewhere on the board
32KHZ_OUT: U100.10 (PC15); also elsewhere on the board
ADC3_3V3: U100.50 (PA4); also elsewhere on the board
ADC3_6V6: U100.34 (PC2); also elsewhere on the board
AGND: U100.37 (VSSA); also elsewhere on the board
BOOT0: U100.166 (BOOT0); also elsewhere on the board
BUZZER_1: U100.27 (PF9)
CAN1_RX: U100.142 (PD0); also elsewhere on the board
CAN1_TX: U100.143 (PD1); also elsewhere on the board
FMU_CAP1: U100.74 (PE11)
FMU_CAP2: U100.41 (PA1)
FMU_CH1: U100.131 (PI0); also elsewhere on the board
FMU_CH2: U100.89 (PH12); also elsewhere on the board
FMU_CH3: U100.88 (PH11); also elsewhere on the board
FMU_CH4: U100.87 (PH10); also elsewhere on the board
FMU_CH5: U100.101 (PD13); also elsewhere on the board
FMU_CH6: U100.104 (PD14); also elsewhere on the board
FMU_CH7: U100.83 (PH6); also elsewhere on the board
FMU_CH8: U100.86 (PH9); also elsewhere on the board
FMU_NSAFETY_SWITCH_LED_OUT: U100.98 (PD10)
FMU_PPM_INPUT: U100.174 (PI5); also elsewhere on the board
FMU_SAFETY_SWITCH_IN: U100.21 (PF5)
FMU_SWCLK: U100.137 (PA14); also elsewhere on the board
FMU_SWDIO: U100.124 (PA13); also elsewhere on the board
GND: U100.14 (VSS), U100.22 (VSS), U100.48 (VSS), U100.61 (VSS), U100.71 (VSS), U100.90 (VSS), U100.102 (VSS), U100.113 (VSS), U100.126 (VSS), U100.135 (VSS), U100.148 (VSS), U100.158 (VSS); also elsewhere on the board
HEATER: U100.42 (PA2)
HW_REV_SENSE: U100.45 (PH4); also elsewhere on the board
HW_VER_REV_DRIVE: U100.66 (PG0); also elsewhere on the board
HW_VER_SENSE: U100.44 (PH3); also elsewhere on the board
I2C1_SCL_BASE_GPS1_MAG_LED_PM1: U100.167 (PB8); also elsewhere on the board
I2C1_SDA_BASE_GPS1_MAG_LED_PM1: U100.168 (PB9); also elsewhere on the board
I2C2_DRDY1_BMP388: U100.109 (PG5); also elsewhere on the board
I2C2_SCL_BASE_GPS2_MAG_LED_PM2: U100.17 (PF1)
I2C2_SDA_BASE_GPS2_MAG_LED_PM2: U100.16 (PF0)
I2C3_SCL_BASE_MS5611_BARBED_EXTERNAL1: U100.119 (PA8); also elsewhere on the board
I2C3_SDA_BASE_MS5611_BARBED_EXTERNAL1: U100.85 (PH8); also elsewhere on the board
I2C4_SCL_FMU: U100.64 (PF14); also elsewhere on the board
I2C4_SDA_FMU: U100.65 (PF15); also elsewhere on the board
MUX_CTRL1: U100.55 (PC5)
MUX_CTRL2: U100.68 (PE7)
NARMED: U100.5 (PE6)
NFC_GPIO: U100.60 (PF12); also elsewhere on the board
NLED_BLUE: U100.4 (PE5); also elsewhere on the board
NLED_GREEN: U100.3 (PE4); also elsewhere on the board
NLED_RED: U100.2 (PE3); also elsewhere on the board
NPOWER_IN_A: U100.67 (PG1)
NPOWER_IN_B: U100.106 (PG2)
NPOWER_IN_C: U100.107 (PG3)
NRST: U100.31 (NRST); also elsewhere on the board
OTG_HS_ULPI_CK: U100.51 (PA5); also elsewhere on the board
OTG_HS_ULPI_D0: U100.47 (PA3); also elsewhere on the board
OTG_HS_ULPI_D1: U100.56 (PB0); also elsewhere on the board
OTG_HS_ULPI_D2: U100.57 (PB1); also elsewhere on the board
OTG_HS_ULPI_D3: U100.79 (PB10); also elsewhere on the board
OTG_HS_ULPI_D4: U100.80 (PB11); also elsewhere on the board
OTG_HS_ULPI_D5__CAN2_RX: U100.92 (PB12); also elsewhere on the board
OTG_HS_ULPI_D6__CAN2_TX: U100.93 (PB13); also elsewhere on the board
OTG_HS_ULPI_D7: U100.163 (PB5); also elsewhere on the board
OTG_HS_ULPI_DIR: U100.13 (PI11); also elsewhere on the board
OTG_HS_ULPI_NXT: U100.35 (PC3); also elsewhere on the board
OTG_HS_ULPI_STP: U100.32 (PC0); also elsewhere on the board
PD15(PH11): U100.105 (PD15); also elsewhere on the board
PDR_ON: U100.171 (PDR_ON); also elsewhere on the board
PF4: U100.20 (PF4)
PG6: U100.110 (PG6)
PG8: U100.112 (PG8)
PG15: U100.160 (PG15)
SCALED_V5: U100.40 (PA0); also elsewhere on the board
SCALED_VDD_3V3_SENSORS: U100.54 (PC4); also elsewhere on the board
SDMMC2_CLK: U100.33 (PC1); also elsewhere on the board
SDMMC2_CMD: U100.151 (PD7); also elsewhere on the board
SDMMC2_D0: U100.94 (PB14); also elsewhere on the board
SDMMC2_D1: U100.95 (PB15); also elsewhere on the board
SDMMC2_D2: U100.161 (PB3); also elsewhere on the board
SDMMC2_D3: U100.162 (PB4); also elsewhere on the board
SPI1_DRDY1_ICM20602: U100.18 (PF2); also elsewhere on the board
SPI1_MISO_SENSOR1_ICM20602: U100.152 (PG9); also elsewhere on the board
SPI1_MOSI_SENSOR1_ICM20602: U100.53 (PA7); also elsewhere on the board
SPI1_NCS1_ICM20602: U100.11 (PI9); also elsewhere on the board
SPI1_SCK_SENSOR1_ICM20602: U100.154 (PG11); also elsewhere on the board
SPI2_DRDY2_ISM330_INT2: U100.121 (PA10); also elsewhere on the board
SPI2_MISO_SENSOR2_ISM330: U100.133 (PI2); also elsewhere on the board
SPI2_MOSI_SENSOR2_ISM330: U100.134 (PI3); also elsewhere on the board
SPI2_NCS1_ISM330: U100.46 (PH5); also elsewhere on the board
SPI2_SCK_SENSOR2_ISM330: U100.132 (PI1); also elsewhere on the board
SPI3_DRDY1_BMI088_INT1_ACCEL: U100.175 (PI6); also elsewhere on the board
SPI3_DRDY2_BMI088_INT3_GYRO: U100.176 (PI7); also elsewhere on the board
SPI3_MISO_SENSOR3_BMI088: U100.140 (PC11); also elsewhere on the board
SPI3_MOSI_SENSOR3_BMI088: U100.58 (PB2); also elsewhere on the board
SPI3_NCS1_BMI088_ACCEL: U100.173 (PI4); also elsewhere on the board
SPI3_NCS2_BMI088_GYRO: U100.7 (PI8); also elsewhere on the board
SPI3_SCK_SENSOR3_BMI088: U100.139 (PC10); also elsewhere on the board
SPI4_DRDY1_BMM150_DRDY: U100.19 (PF3); also elsewhere on the board
SPI4_MISO_SENSOR4_BMM150: U100.76 (PE13); also elsewhere on the board
SPI4_MOSI_SENSOR4_BMM150: U100.77 (PE14); also elsewhere on the board
SPI4_NCS1_BMM150: U100.130 (PH15); also elsewhere on the board
SPI4_SCK_SENSOR4_BMM150: U100.75 (PE12); also elsewhere on the board
SPI5_MISO_FRAM: U100.84 (PH7); also elsewhere on the board
SPI5_MOSI_FRAM: U100.59 (PF11); also elsewhere on the board
SPI5_NCS1_FRAM: U100.111 (PG7); also elsewhere on the board
SPI5_SCK_FRAM: U100.25 (PF7); also elsewhere on the board
SPI6_DRDY1_EXTERNAL1: U100.99 (PD11)
SPI6_DRDY2_EXTERNAL1: U100.100 (PD12)
SPI6_MISO_EXTERNAL1: U100.52 (PA6)
SPI6_MOSI_EXTERNAL1: U100.157 (PG14)
SPI6_NCS1_EXTERNAL1: U100.12 (PI10)
SPI6_NCS2_EXTERNAL1: U100.138 (PA15)
SPI6_NRESET_EXTERNAL1: U100.28 (PF10)
SPI6_SCK_EXTERNAL1: U100.156 (PG13); also elsewhere on the board
SPIX_SYNC: U100.70 (PE9)
TRACECLK: U100.1 (PE2)
UART4_RX: U100.129 (PH14)
UART4_TX: U100.128 (PH13)
UART5_CTS_TELEM2: U100.118 (PC9); also elsewhere on the board
UART5_RTS_TELEM2: U100.117 (PC8); also elsewhere on the board
UART5_RX_TELEM2: U100.144 (PD2); also elsewhere on the board
UART5_TX_TELEM2: U100.141 (PC12); also elsewhere on the board
UART7_CTS_TELEM1: U100.73 (PE10)
UART7_RTS_TELEM1: U100.26 (PF8)
UART7_RX_TELEM1: U100.24 (PF6)
UART7_TX_TELEM1: U100.69 (PE8)
UART8_RX_GPS2: U100.169 (PE0)
UART8_TX_GPS2: U100.170 (PE1)
USART1_RX_GPS1: U100.165 (PB7); also elsewhere on the board
USART1_TX_GPS1: U100.164 (PB6); also elsewhere on the board
USART2_CTS_TELEM3: U100.145 (PD3)
USART2_RTS_TELEM3: U100.146 (PD4)
USART2_RX_TELEM3: U100.150 (PD6)
USART3_RX_DEBUG: U100.97 (PD9); also elsewhere on the board
USART3_TX_DEBUG: U100.96 (PD8); also elsewhere on the board
USART6_RX_FROM_IO__RC_INPUT: U100.116 (PC7); also elsewhere on the board
USART6_TX_TO_IO__NC: U100.115 (PC6)
USB_D_N: U100.122 (PA11); also elsewhere on the board
USB_D_P: U100.123 (PA12); also elsewhere on the board
VBAT: U100.6 (VBAT); also elsewhere on the board
VBUS_SENSE: U100.120 (PA9); also elsewhere on the board
VCAP: U100.81 (VCAP), U100.125 (VCAP); also elsewhere on the board
VDDA: U100.39 (VDDA); also elsewhere on the board
VDD_3V3_SD_CARD_EN: U100.8 (PC13); also elsewhere on the board
VDD_3V3_SENSORS_EN: U100.155 (PG12); also elsewhere on the board
VDD_3V3_SPEKTRUM_POWER_EN: U100.43 (PH2); also elsewhere on the board
VDD_5V_HIPOWER_NEN: U100.153 (PG10); also elsewhere on the board
VDD_5V_HIPOWER_NOC: U100.63 (PF13); also elsewhere on the board
VDD_5V_PERIPH_NEN: U100.108 (PG4); also elsewhere on the board
VDD_5V_PERIPH_NOC: U100.78 (PE15); also elsewhere on the board
VREFP: U100.38 (VREF+); also elsewhere on the board

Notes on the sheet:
STM32H753

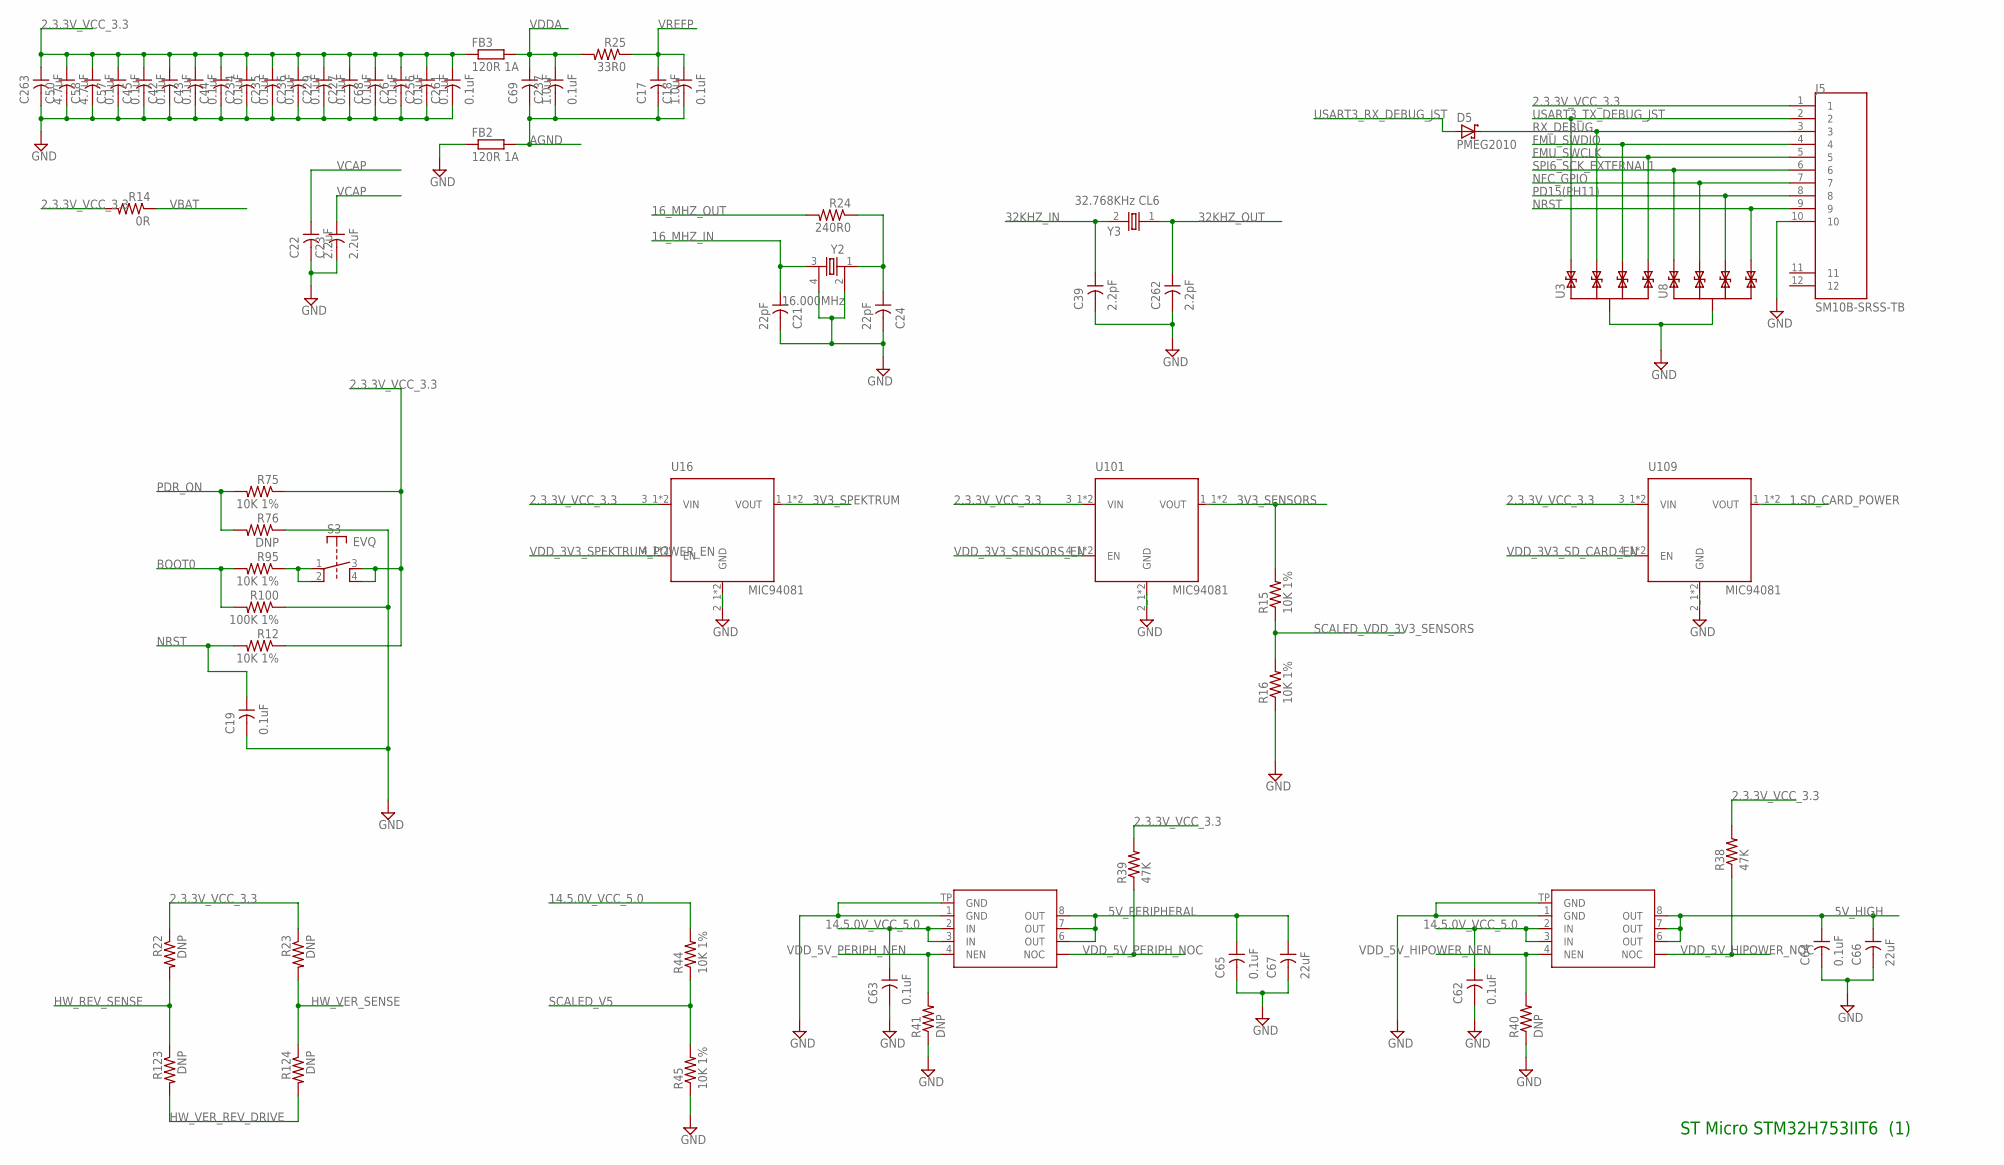
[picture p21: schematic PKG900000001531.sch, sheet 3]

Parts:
C17, C69: 1.0uF; 0402
C18, C19, C26, C42, C43, C44, C45, C57, C58, C62, C63, C64, C65, C68, C227, C229, C234, C235, C236, C237, C256, C261: 0.1uF; 0201
C21, C24: 22pF; 0201
C22, C23: 2.2uF; 0603
C39, C262: 2.2pF; 0201
C50, C263: 4.7uF; 0603
C66, C67: 22uF; 0805
D5: PMEG2010; SOD123F
FB2, FB3: 120R 1A; 0402
J5: SM10B-SRSS-TB
R12, R15, R16, R44, R45, R75, R95: 10K 1%; 0201
R14: 0R; 0402
R22, R23, R40, R41, R76, R123, R124: DNP; 0201
R24: 240R0; 0201
R25: 33R0; 0201
R38, R39: 47K; 0201
R100: 100K 1%; 0201
S3: EVQ; KMT0
U1, U25: TPS2041BDGN; MSOP8-PAD
U3, U8: TPD4E02B0410-USON; UFDFN-10
U16, U101, U109: MIC94081; FTDFN-4
Y2: 16.000MHz; CRYSTAL-3225
Y3: 32.768KHz CL6; 1206

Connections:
1.SD_CARD_POWER: U109.1_1 (VOUT), U109.1_2 (VOUT); also elsewhere on the board
2.3.3V_VCC_3.3: C26.1, C42.1, C43.1, C44.1, C45.1, C50.1, C57.1, C58.1, C68.1, C227.1, C229.1, C234.1, C235.1, C236.1, C256.1, C261.1, C263.1, FB3.1, J5.1, R12.1, R14.2, R22.1, R23.1, R38.2, R39.2, R75.1, S3.3 (B), S3.4 (B'), U16.3_1 (VIN), U16.3_2 (VIN), U101.3_1 (VIN), U101.3_2 (VIN), U109.3_1 (VIN), U109.3_2 (VIN); also elsewhere on the board
3V3_SENSORS: R15.2, U101.1_1 (VOUT), U101.1_2 (VOUT); also elsewhere on the board
3V3_SPEKTRUM: U16.1_1 (VOUT), U16.1_2 (VOUT); also elsewhere on the board
5V_HIGH: C64.1, C66.1, U25.6 (OUT), U25.7 (OUT), U25.8 (OUT); also elsewhere on the board
5V_PERIPHERAL: C65.1, C67.1, U1.6 (OUT), U1.7 (OUT), U1.8 (OUT); also elsewhere on the board
14.5.0V_VCC_5.0: C62.1, C63.1, R44.2, U1.2 (IN), U1.3 (IN), U25.2 (IN), U25.3 (IN); also elsewhere on the board
16_MHZ_IN: C21.1, Y2.3; also elsewhere on the board
16_MHZ_OUT: R24.2; also elsewhere on the board
32KHZ_IN: C39.1, Y3.2; also elsewhere on the board
32KHZ_OUT: C262.1, Y3.1; also elsewhere on the board
AGND: C17.2, C18.2, C69.2, C237.2, FB2.2; also elsewhere on the board
BOOT0: R95.2, R100.2; also elsewhere on the board
BOOTBUT$1: R95.1, S3.1 (A), S3.2 (A')
FMU_SWCLK: J5.5, U3.5 (P4), U3.6 (P4); also elsewhere on the board
FMU_SWDIO: J5.4, U3.4 (P3), U3.7 (P3); also elsewhere on the board
GND: C19.2, C21.2, C22.2, C23.2, C24.2, C26.2, C39.2, C42.2, C43.2, C44.2, C45.2, C50.2, C57.2, C58.2, C62.2, C63.2, C64.2, C65.2, C66.2, C67.2, C68.2, C227.2, C229.2, C234.2, C235.2, C236.2, C256.2, C261.2, C262.2, C263.2, FB2.1, J5.10, R16.1, R40.1, R41.1, R45.1, R76.1, R100.1, U1.1 (GND), U1.TP (GND), U3.3 (SHIELD), U3.8 (SHIELD), U8.3 (SHIELD), U8.8 (SHIELD), U16.2_1 (GND), U16.2_2 (GND), U25.1 (GND), U25.TP (GND), U101.2_1 (GND), U101.2_2 (GND), U109.2_1 (GND), U109.2_2 (GND), Y2.2, Y2.4; also elsewhere on the board
HW_REV_SENSE: R22.2, R123.1; also elsewhere on the board
HW_VER_REV_DRIVE: R123.2, R124.2; also elsewhere on the board
HW_VER_SENSE: R23.2, R124.1; also elsewhere on the board
NFC_GPIO: J5.7, U8.2, U8.9 (P2); also elsewhere on the board
NRST: C19.1, J5.9, R12.2, U8.5 (P4), U8.6 (P4); also elsewhere on the board
PD15(PH11): J5.8, U8.4 (P3), U8.7 (P3); also elsewhere on the board
PDR_ON: R75.2, R76.2; also elsewhere on the board
RX_DEBUG: D5.C, J5.3, U3.2, U3.9 (P2)
SCALED_V5: R44.1, R45.2; also elsewhere on the board
SCALED_VDD_3V3_SENSORS: R15.1, R16.2; also elsewhere on the board
SPI6_SCK_EXTERNAL1: J5.6, U8.1, U8.10 (P1); also elsewhere on the board
STM_OSC2$1: C24.1, R24.1, Y2.1
USART3_RX_DEBUG_JST: D5.A; also elsewhere on the board
USART3_TX_DEBUG_JST: J5.2, U3.1, U3.10 (P1); also elsewhere on the board
VBAT: R14.1; also elsewhere on the board
VCAP: C22.1, C23.1; also elsewhere on the board
VDDA: C69.1, C237.1, FB3.2, R25.2; also elsewhere on the board
VDD_3V3_SD_CARD_EN: U109.4_1 (EN), U109.4_2 (EN); also elsewhere on the board
VDD_3V3_SENSORS_EN: U101.4_1 (EN), U101.4_2 (EN); also elsewhere on the board
VDD_3V3_SPEKTRUM_POWER_EN: U16.4_1 (EN), U16.4_2 (EN); also elsewhere on the board
VDD_5V_HIPOWER_NEN: R40.2, U25.4 (NEN); also elsewhere on the board
VDD_5V_HIPOWER_NOC: R38.1, U25.5 (NOC); also elsewhere on the board
VDD_5V_PERIPH_NEN: R41.2, U1.4 (NEN); also elsewhere on the board
VDD_5V_PERIPH_NOC: R39.1, U1.5 (NOC); also elsewhere on the board
VREFP: C17.1, C18.1, R25.1; also elsewhere on the board

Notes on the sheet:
ST Micro STM32H753IIT6 (1)

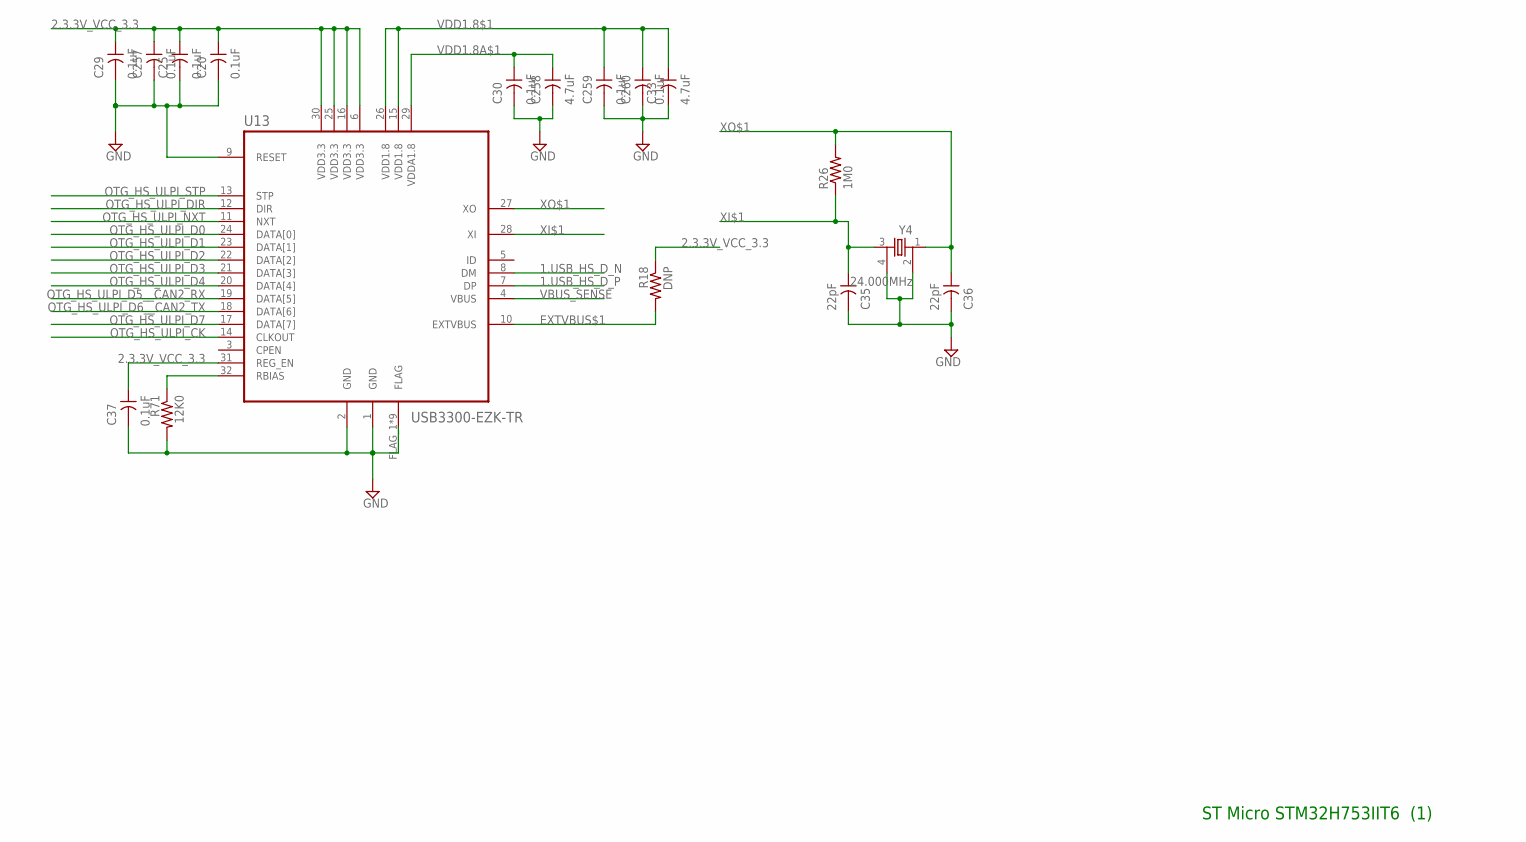
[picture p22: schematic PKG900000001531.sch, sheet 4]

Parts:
C20, C25, C29, C30, C37, C257, C259, C260: 0.1uF; 0201
C33, C258: 4.7uF; 0603
C35, C36: 22pF; 0201
R18: DNP; 0201
R26: 1M0; 0402
R71: 12K0; 0402
U13: USB3300-EZK-TR; QFN32-USB3300
Y4: 24.000MHz; CRYSTAL-3225

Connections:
1.USB_HS_D_N: U13.8 (DM); also elsewhere on the board
1.USB_HS_D_P: U13.7 (DP); also elsewhere on the board
2.3.3V_VCC_3.3: C20.1, C25.1, C29.1, C37.1, C257.1, R18.1, U13.6 (VDD3.3), U13.16 (VDD3.3), U13.25 (VDD3.3), U13.30 (VDD3.3), U13.31 (REG_EN); also elsewhere on the board
EXTVBUS$1: R18.2, U13.10 (EXTVBUS)
GND: C20.2, C25.2, C29.2, C30.2, C33.2, C35.2, C36.2, C37.2, C257.2, C258.2, C259.2, C260.2, R71.2, U13.1 (GND), U13.2 (GND), U13.9 (RESET), U13.FLAG_1 (FLAG), U13.FLAG_2 (FLAG), U13.FLAG_3 (FLAG), U13.FLAG_4 (FLAG), U13.FLAG_5 (FLAG), U13.FLAG_6 (FLAG), U13.FLAG_7 (FLAG), U13.FLAG_8 (FLAG), U13.FLAG_9 (FLAG), Y4.2, Y4.4; also elsewhere on the board
OTG_HS_ULPI_CK: U13.14 (CLKOUT); also elsewhere on the board
OTG_HS_ULPI_D0: U13.24 (DATA[0]); also elsewhere on the board
OTG_HS_ULPI_D1: U13.23 (DATA[1]); also elsewhere on the board
OTG_HS_ULPI_D2: U13.22 (DATA[2]); also elsewhere on the board
OTG_HS_ULPI_D3: U13.21 (DATA[3]); also elsewhere on the board
OTG_HS_ULPI_D4: U13.20 (DATA[4]); also elsewhere on the board
OTG_HS_ULPI_D5__CAN2_RX: U13.19 (DATA[5]); also elsewhere on the board
OTG_HS_ULPI_D6__CAN2_TX: U13.18 (DATA[6]); also elsewhere on the board
OTG_HS_ULPI_D7: U13.17 (DATA[7]); also elsewhere on the board
OTG_HS_ULPI_DIR: U13.12 (DIR); also elsewhere on the board
OTG_HS_ULPI_NXT: U13.11 (NXT); also elsewhere on the board
OTG_HS_ULPI_STP: U13.13 (STP); also elsewhere on the board
RBIAS$1: R71.1, U13.32 (RBIAS)
VBUS_SENSE: U13.4 (VBUS); also elsewhere on the board
VDD1.8$1: C33.1, C259.1, C260.1, U13.15 (VDD1.8), U13.26 (VDD1.8)
VDD1.8A$1: C30.1, C258.1, U13.29 (VDDA1.8)
XI$1: C35.1, R26.1, U13.28 (XI), Y4.3
XO$1: C36.1, R26.2, U13.27 (XO), Y4.1

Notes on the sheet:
ST Micro STM32H753IIT6 (1)

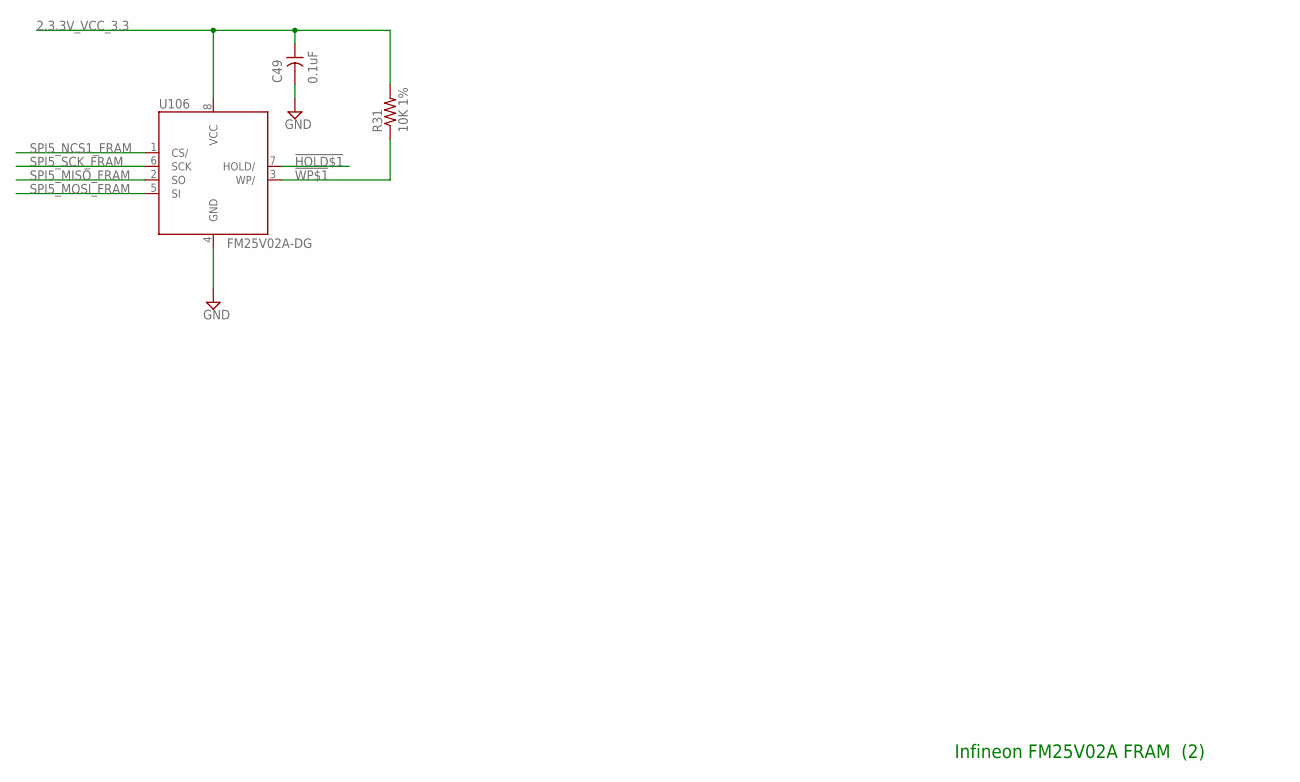
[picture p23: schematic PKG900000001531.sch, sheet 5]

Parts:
C49: 0.1uF; 0201
R31: 10K 1%; 0201
U106: FM25V02A-DG; DFN8-4X4.5

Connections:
2.3.3V_VCC_3.3: C49.1, R31.2, U106.8 (VCC); also elsewhere on the board
!HOLD$1: U106.7 (HOLD/)
!WP$1: R31.1, U106.3 (WP/)
GND: C49.2, U106.4 (GND); also elsewhere on the board
SPI5_MISO_FRAM: U106.2 (SO); also elsewhere on the board
SPI5_MOSI_FRAM: U106.5 (SI); also elsewhere on the board
SPI5_NCS1_FRAM: U106.1 (CS/); also elsewhere on the board
SPI5_SCK_FRAM: U106.6 (SCK); also elsewhere on the board

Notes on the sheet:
Infineon FM25V02A FRAM (2)

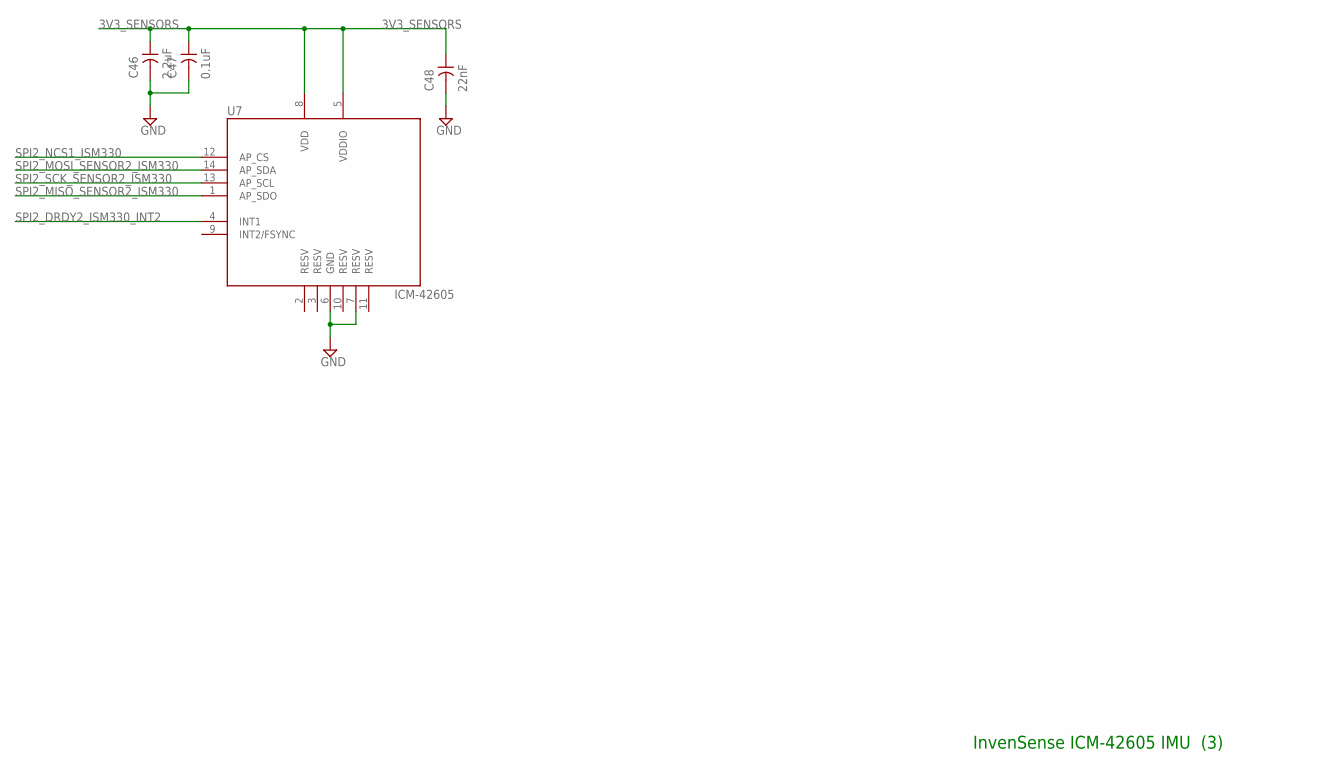
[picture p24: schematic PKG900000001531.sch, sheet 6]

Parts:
C46: 2.2uF; 0402
C47: 0.1uF; 0201
C48: 22nF; 0201
U7: ICM-42605; LGA14-2.5X3MM

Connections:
3V3_SENSORS: C46.1, C47.1, C48.1, U7.5 (VDDIO), U7.8 (VDD); also elsewhere on the board
GND: C46.2, C47.2, C48.2, U7.6 (GND), U7.7 (RESV); also elsewhere on the board
SPI2_DRDY2_ISM330_INT2: U7.4 (INT1); also elsewhere on the board
SPI2_MISO_SENSOR2_ISM330: U7.1 (AP_SDO); also elsewhere on the board
SPI2_MOSI_SENSOR2_ISM330: U7.14 (AP_SDA); also elsewhere on the board
SPI2_NCS1_ISM330: U7.12 (AP_CS); also elsewhere on the board
SPI2_SCK_SENSOR2_ISM330: U7.13 (AP_SCL); also elsewhere on the board

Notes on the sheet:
InvenSense ICM-42605 IMU (3)

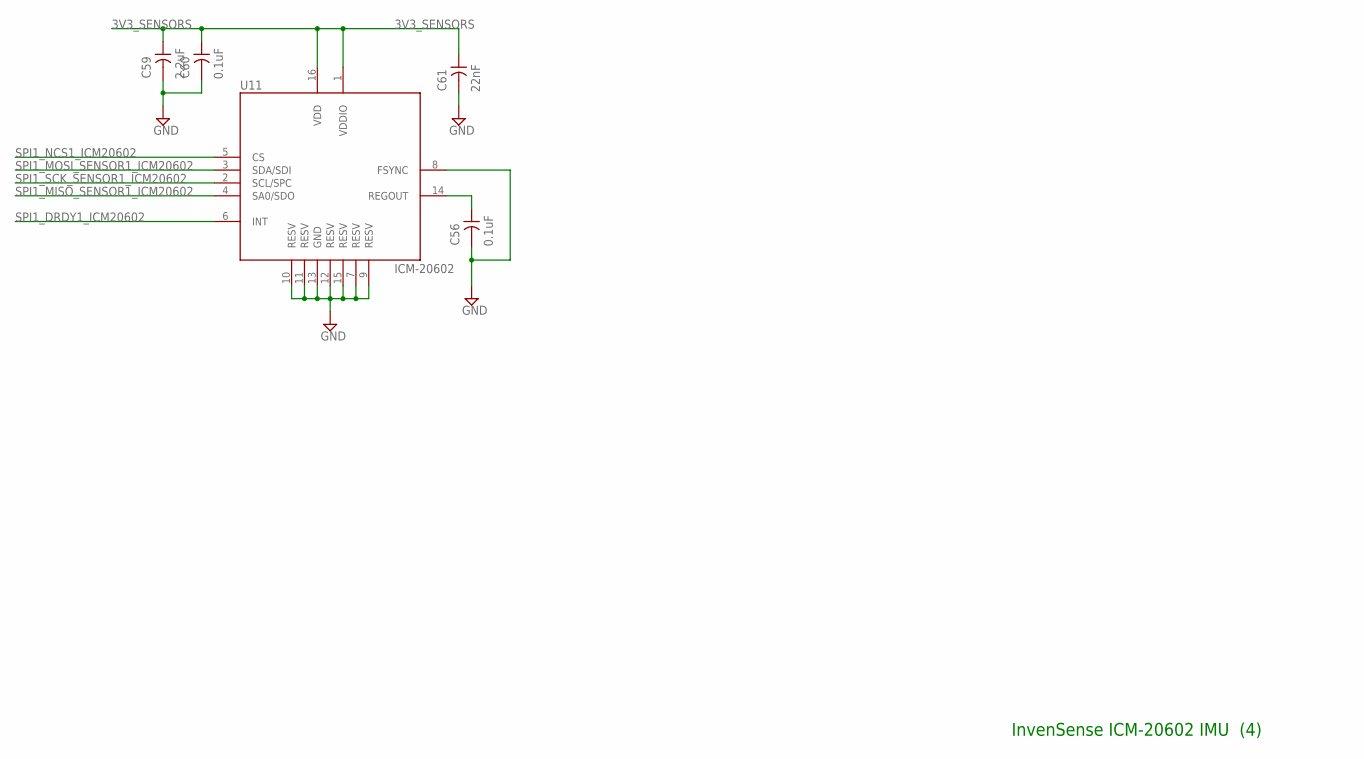
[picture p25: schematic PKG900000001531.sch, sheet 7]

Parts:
C56, C60: 0.1uF; 0201
C59: 2.2uF; 0402
C61: 22nF; 0201
U11: ICM-20602; LGA16-3X3MM

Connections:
3V3_SENSORS: C59.1, C60.1, C61.1, U11.1 (VDDIO), U11.16 (VDD); also elsewhere on the board
GND: C56.2, C59.2, C60.2, C61.2, U11.7 (RESV), U11.8 (FSYNC), U11.9 (RESV), U11.10 (RESV), U11.11 (RESV), U11.12 (RESV), U11.13 (GND), U11.15 (RESV); also elsewhere on the board
REGOUT$1: C56.1, U11.14 (REGOUT)
SPI1_DRDY1_ICM20602: U11.6 (INT); also elsewhere on the board
SPI1_MISO_SENSOR1_ICM20602: U11.4 (SA0/SDO); also elsewhere on the board
SPI1_MOSI_SENSOR1_ICM20602: U11.3 (SDA/SDI); also elsewhere on the board
SPI1_NCS1_ICM20602: U11.5 (CS); also elsewhere on the board
SPI1_SCK_SENSOR1_ICM20602: U11.2 (SCL/SPC); also elsewhere on the board

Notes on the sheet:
InvenSense ICM-20602 IMU (4)

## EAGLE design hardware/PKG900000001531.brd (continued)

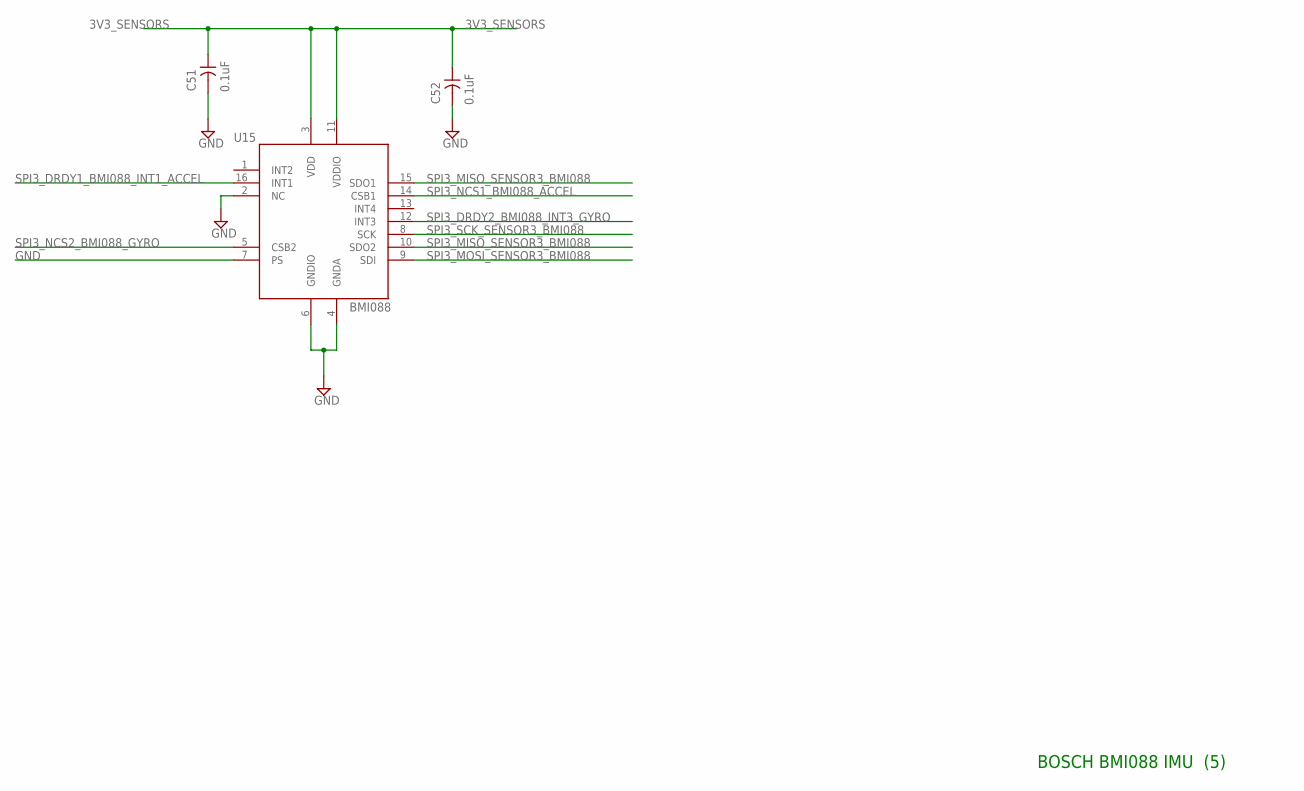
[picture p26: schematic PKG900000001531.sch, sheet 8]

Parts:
C51, C52: 0.1uF; 0201
U15: BMI088; LGA16-BMI088

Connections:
3V3_SENSORS: C51.1, C52.1, U15.3 (VDD), U15.11 (VDDIO); also elsewhere on the board
GND: C51.2, C52.2, U15.2 (NC), U15.4 (GNDA), U15.6 (GNDIO), U15.7 (PS); also elsewhere on the board
SPI3_DRDY1_BMI088_INT1_ACCEL: U15.16 (INT1); also elsewhere on the board
SPI3_DRDY2_BMI088_INT3_GYRO: U15.12 (INT3); also elsewhere on the board
SPI3_MISO_SENSOR3_BMI088: U15.10 (SDO2), U15.15 (SDO1); also elsewhere on the board
SPI3_MOSI_SENSOR3_BMI088: U15.9 (SDI); also elsewhere on the board
SPI3_NCS1_BMI088_ACCEL: U15.14 (CSB1); also elsewhere on the board
SPI3_NCS2_BMI088_GYRO: U15.5 (CSB2); also elsewhere on the board
SPI3_SCK_SENSOR3_BMI088: U15.8 (SCK); also elsewhere on the board

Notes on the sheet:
BOSCH BMI088 IMU (5)

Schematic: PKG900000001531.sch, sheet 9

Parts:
C53, C55: 0.1uF; 0201
R13, R47, R77: 10K 1%; 0201
R17, R46, R86, R87, R88: DNP; 0201
R90, R107: 0R; 0201
R108, R109: 1K5; 0201
U9: BMM150; WLCSP-12

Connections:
3V3_SENSORS: C53.1, C55.1, R47.2, R108.1, R109.1, U9.B2 (VDDIO), U9.E5 (VDD); also elsewhere on the board
BMM150_PS: R46.2, R47.1, U9.A1 (PS)
CSB$1: R77.2, R87.2, U9.A5 (CSB)
GND: C53.2, C55.2, R13.1, R46.1, R77.1, U9.C5 (GND), U9.E1 (GND), U9.E3 (GND); also elsewhere on the board
I2C4_SCL_FMU: R107.2, R109.2; also elsewhere on the board
I2C4_SDA_FMU: R90.2, R108.2; also elsewhere on the board
SCK$1: R17.1, R107.1, U9.A3 (SCK)
SDI$1: R88.1, R90.1, U9.B4 (SDI)
SDO$1: R13.2, R86.2, U9.C1 (SDO)
SPI4_DRDY1_BMM150_DRDY: U9.D4 (DRDY); also elsewhere on the board
SPI4_MISO_SENSOR4_BMM150: R86.1; also elsewhere on the board
SPI4_MOSI_SENSOR4_BMM150: R88.2; also elsewhere on the board
SPI4_NCS1_BMM150: R87.1; also elsewhere on the board
SPI4_SCK_SENSOR4_BMM150: R17.2; also elsewhere on the board

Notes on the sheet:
Bosch BMM150 Magnetometer (6)

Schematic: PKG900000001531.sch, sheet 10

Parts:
C54: DNP; 0201
C70, C71: 0.1uF; 0201
R51, R53, R57, R59: DNP; 0201
U10: DNP; BA03
U108: BMP388; LGA10

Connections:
3V3_SENSORS: C54.1, C70.1, C71.1, R53.1, R57.1, R59.2, U10.1 (VDD), U108.1 (VDDIO), U108.6 (CSB), U108.10 (VDD); also elsewhere on the board
GND: C54.2, C70.2, C71.2, R51.1, U10.3 (GND), U108.3 (VSS), U108.5 (SDO), U108.8 (VSS), U108.9 (VSS); also elsewhere on the board
I2C2_DRDY1_BMP388: U108.7 (INT); also elsewhere on the board
I2C3_SCL_BASE_MS5611_BARBED_EXTERNAL1: R57.2, U10.8 (SCLK); also elsewhere on the board
I2C3_SDA_BASE_MS5611_BARBED_EXTERNAL1: R53.2, U10.7 (SDA); also elsewhere on the board
I2C4_SCL_FMU: U108.2 (SCK); also elsewhere on the board
I2C4_SDA_FMU: U108.4 (SDI); also elsewhere on the board
MS5611_CS$1: R51.2, U10.4 (CSB)
MS5611_PS$1: R59.1, U10.2 (PS)

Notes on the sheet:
BMP388 & MS5611 Barometer (7)

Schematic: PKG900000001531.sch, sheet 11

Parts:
D2: EAST1616RGBB4; SMD4
R78: 196R; 0201
R79, R85: 100R; 0201

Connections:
2.3.3V_VCC_3.3: D2.4 (VCC); also elsewhere on the board
C_BLUE$1: D2.3 (B), R85.1
C_GREEN$1: D2.2 (G), R79.1
C_RED$1: D2.1 (R), R78.1
NLED_BLUE: R85.2; also elsewhere on the board
NLED_GREEN: R79.2; also elsewhere on the board
NLED_RED: R78.2; also elsewhere on the board

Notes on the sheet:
Discrete RGB LED (16)

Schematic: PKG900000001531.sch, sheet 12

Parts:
C228: 0.1uF / 16V; 0402
C230: 10uF / 16V; 0805
C231: 1.0uF; 0402
C232: 10pF; 0201
C233: 22uF; 0805
IC3: TPS62111; PQFP16
L1: 6.8uH; 1515
R80: 1M0; 0201
R81: 0R; 0402
R83: DNP; 0402

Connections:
2.3.3V_VCC_3.3: C232.1, C233.1, L1.2, R80.2, R81.2; also elsewhere on the board
14.5.0V_VCC_5.0: C228.1, C230.1, C231.1, IC3.2 (VIN), IC3.3 (VIN), IC3.4 (EN), IC3.8 (VIN); also elsewhere on the board
FB_3.3$2: C232.2, IC3.10 (FB), R81.1, R83.2
GND: C228.2, C230.2, C231.2, C233.2, IC3.1 (PGND), IC3.5 (SYNC), IC3.6 (LBO), IC3.7 (LBI), IC3.9 (GND), IC3.11 (GND), IC3.12 (GND), IC3.16 (PGND), IC3.P$1 (GND), R83.1; also elsewhere on the board
PG_3.3$2: IC3.13 (PG), R80.1
SW_3.3$2: IC3.14 (SW), IC3.15 (SW), L1.1

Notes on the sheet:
3.3V 1500mA Buck

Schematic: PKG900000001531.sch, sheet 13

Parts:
C226: 1.0uF; 0402
J7: USB-TYPE-C; USB-TYPE-C-SMT
L9: DLP11SN900HL2; 0504-DLP11S
R68, R89: 5K1; 0201
R82: 0R; 0201
U107: TPD4E02B0410-USON; UFDFN-10

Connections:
3.5.0V_VCC_5.0: C226.1, J7.A4 (VBUS), J7.A9 (VBUS), J7.B4 (VBUS), J7.B9 (VBUS), R82.2, U107.5 (P4), U107.6 (P4); also elsewhere on the board
4.USB_D_N: L9.3; also elsewhere on the board
4.USB_D_P: L9.2; also elsewhere on the board
CC1$3: J7.A5 (CC1), R68.2
CC2$3: J7.B5 (CC2), R89.2
COMMON_SHIELD: J7.P$1 (SHIELD), J7.P$2 (SHIELD), J7.P$3 (SHIELD), J7.P$4 (SHIELD), U107.3 (SHIELD), U107.8 (SHIELD)
D_N$3: J7.A7 (D-), J7.B7 (D-), L9.4, U107.1, U107.10 (P1)
D_P$3: J7.A6 (D+), J7.B6 (D+), L9.1, U107.2, U107.9 (P2)
GND: C226.2, J7.A1 (GND), J7.A12 (GND), J7.B1 (GND), J7.B12 (GND), R68.1, R89.1; also elsewhere on the board
RX1_N$3: J7.B10 (RX1-)
RX1_P$3: J7.B11 (RX1+)
RX2_N$3: J7.A10 (RX2-)
RX2_P$3: J7.A11 (RX2+)
TX1_N$3: J7.A3 (TX1-)
TX1_P$3: J7.A2 (TX1+)
TX2_N$3: J7.B3 (TX2-)
TX2_P$3: J7.B2 (TX2+)
VBUS_SENSE: R82.1; also elsewhere on the board

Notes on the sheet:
USB Type-C PD (5V)
Pull both CC pins low with 5.1K 1% to enable UFP and PD.

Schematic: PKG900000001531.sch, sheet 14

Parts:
C7, C13, C95, C97, C238, C239, C240, C241, C248: 0.1uF; 0201
C8, C31, C96: 1.0uF; 0402
C9: 4.7uF; 0603
C10, C11: 22pF; 0201
C12: 0.1uF; 0402
R5, R91, R92, R93, R97, R98, R99: 100K 1%; 0201
R96: 1M0; 0201
R102: 12K0; 0201
U14: USB2517-JZX; QFN64-9X9MM-FT2232HQ
Y1: 24.000MHz; CRYSTAL-3225

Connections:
1.USB_HS_D_N: U14.1 (USBDN1_DM/PRT_DIS_M1); also elsewhere on the board
1.USB_HS_D_P: U14.2 (USBDN1_DP/PRT_DIS_P1); also elsewhere on the board
2.3.3V_VCC_3.3: C7.1, C8.1, C9.1, C13.1, C238.1, C239.1, C240.1, C241.1, C248.1, R5.1, R91.1, R97.1, R98.2, U14.5 (VDDA33_2), U14.10 (VDDA33_4), U14.24 (VDD33CR), U14.46 (VDD33), U14.52 (VDDA33_3), U14.57 (VDDA33), U14.64 (VDD33PLL); also elsewhere on the board
4.USB_D_N: U14.58 (USBUP_DM); also elsewhere on the board
4.USB_D_P: U14.59 (USBUP_DP); also elsewhere on the board
5.USB_DEVICE_D_N: U14.53 (USBDN6_DM/PRT_DIS_M6); also elsewhere on the board
5.USB_DEVICE_D_P: U14.54 (USBDN6_DP/PRT_DIS_P6); also elsewhere on the board
6.USB_DEVICE_D_N: U14.55 (USBDN7_DM/PRT_DIS_M7); also elsewhere on the board
6.USB_DEVICE_D_P: U14.56 (USBDN7_DP/PRT_DIS_P7); also elsewhere on the board
CFG_SEL2$: R5.2, U14.13 (CFG_SEL2)
CORAL_D_N: U14.11 (USBDN5_DM/PRT_DIS_M5); also elsewhere on the board
CORAL_D_P: U14.12 (USBDN5_DP/PRT_DIS_P5); also elsewhere on the board
GND: C7.2, C8.2, C9.2, C10.2, C11.2, C12.2, C13.2, C31.2, C95.2, C96.2, C97.2, C238.2, C239.2, C240.2, C241.2, C248.2, R92.1, R93.1, R99.1, R102.1, U14.19 (TEST), U14.65 (EPAD), U14.EPAD1 (EPAD), U14.EPAD2 (EPAD), U14.EPAD3 (EPAD), U14.EPAD4 (EPAD), U14.EPAD5 (EPAD), U14.EPAD6 (EPAD), U14.EPAD7 (EPAD), U14.EPAD8 (EPAD), U14.EPAD9 (EPAD), U14.EPAD10 (EPAD), U14.EPAD11 (EPAD), U14.EPAD12 (EPAD), Y1.2, Y1.4; also elsewhere on the board
USB_CRFILT$: C31.1, C95.1, U14.25 (VDD18)
USB_D_N: U14.3 (USBDN2_DM/PRT_DIS_M2); also elsewhere on the board
USB_D_P: U14.4 (USBDN2_DP/PRT_DIS_P2); also elsewhere on the board
USB_HS_IND$4: R91.2, U14.42 (HS_IND/CFG_SEL1)
USB_NRESET$4: C12.1, R98.1, U14.43 (RESET_N)
USB_PLLFILT$: C96.1, C97.1, U14.62 (VDD18PLL)
USB_RBIAS$4: R102.2, U14.63 (RBIAS)
USB_SCL$4: R99.2, U14.41 (SCL/SMBCLK/CFG_SEL0)
USB_SDA$4: R93.2, U14.40 (SDA/SMBDATA/NON_REM1)
USB_SUSP_IND$4: R92.2, U14.45 (SUSP_IND/LOCAL_PWR/NON_REM0)
USB_XTAL1$4: C11.1, R96.2, U14.61 (XTAL1/CLKIN), Y1.3
USB_XTAL2$4: C10.1, R96.1, U14.60 (XTAL2), Y1.1
VBUS_DET$: R97.2, U14.44 (VBUS_DET)

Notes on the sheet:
7-Port USB Client Hub

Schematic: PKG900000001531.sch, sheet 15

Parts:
C243, C244, C245, C247: 0.1uF; 0201
C246: 4.7uF; 0603
FB4: 120R 1A; 0402
IC5: FT232RQ; QFN32
IC6: SN74LVC1G126DCKR; SC70-5
R55, R56: 10K 1%; 0201
U30: TS3A5223; UQFN-10

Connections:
2.3.3V_VCC_3.3: C243.1, C247.1, IC5.1 (VCCIO), IC6.1 (OE), IC6.5 (VCC), U30.1 (VCC); also elsewhere on the board
5.USB_DEVICE_D_N: IC5.15 (USBDM); also elsewhere on the board
5.USB_DEVICE_D_P: IC5.14 (USBDP); also elsewhere on the board
FTDI_3.3_INT$5: C244.1, IC5.16 (3V3OUT)
GND: C243.2, C244.2, C245.2, C246.2, C247.2, IC5.4 (GND), IC5.17 (GND), IC5.20 (GND), IC5.24 (GND), IC5.26 (TEST), IC6.3 (GND), R56.1, U30.6 (GND); also elsewhere on the board
RX_SW$5: IC5.30 (TXD), IC6.2 (I)
UART_MUX_SEL$: R55.1, R56.2, U30.4 (SEL1), U30.8 (SEL2)
USART3_RX_DEBUG: U30.3 (COM1); also elsewhere on the board
USART3_RX_DEBUG_FTDI: IC6.4 (O), U30.2 (NO1)
USART3_RX_DEBUG_JST: U30.5 (NC1); also elsewhere on the board
USART3_TX_DEBUG: U30.9 (COM2); also elsewhere on the board
USART3_TX_DEBUG_FTDI: IC5.2 (RXD), U30.10 (NO2)
USART3_TX_DEBUG_JST: U30.7 (NC2); also elsewhere on the board
VBUS$5: C245.1, C246.1, FB4.2, IC5.18 (!RESET), IC5.19 (VCC)
VBUS_SENSE: FB4.1, R55.2; also elsewhere on the board

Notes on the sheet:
USB to UART

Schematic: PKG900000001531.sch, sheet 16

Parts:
C4, C5, C249, C253: 0.1uF; 0201
C250: 4.7uF; 0603
FB1: 120R 1A; 0402
IC2: FT232RQ; QFN32
IC7: SN74LVC1G126DCKR; SC70-5

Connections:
6.USB_DEVICE_D_N: IC2.15 (USBDM); also elsewhere on the board
6.USB_DEVICE_D_P: IC2.14 (USBDP); also elsewhere on the board
7.UART0_RXD: IC7.4 (O); also elsewhere on the board
7.UART0_TXD: IC2.2 (RXD); also elsewhere on the board
7.VLOGIC_VLOGIC: C4.1, C249.1, IC2.1 (VCCIO), IC7.1 (OE), IC7.5 (VCC); also elsewhere on the board
FTDI_3.3_INT$6: C5.1, IC2.16 (3V3OUT)
GND: C4.2, C5.2, C249.2, C250.2, C253.2, IC2.4 (GND), IC2.17 (GND), IC2.20 (GND), IC2.24 (GND), IC2.26 (TEST), IC7.3 (GND); also elsewhere on the board
RX_SW$6: IC2.30 (TXD), IC7.2 (I)
VBUS$6: C250.1, C253.1, FB1.2, IC2.18 (!RESET), IC2.19 (VCC)
VBUS_SENSE: FB1.1; also elsewhere on the board

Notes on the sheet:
USB to UART

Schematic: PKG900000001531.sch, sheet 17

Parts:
J2, J8: DF40HC(3.0)-100DS-0.4V(51); HRS_DF40C-100DS-0.4V(51)
MP1, MP2, MP3, MP4: 9774030151R; WA-SMSI_9774___151
Q1, Q3, Q4, Q6: FDN360P; SOT23
Q5: BSS138; SOT23
R9, R42, R101, R113: 0R; 0201
R103: 10K 1%; 0201
R106: DNP; 0201

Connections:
1.8V_OUT$7: J8.88, J8.90, Q1.3 (D), R106.1
3.3V_OUT$7: J8.84, J8.86, Q4.3 (D), R101.1
7.1.8V_VCC_1.8: Q6.3 (D); also elsewhere on the board
7.3.3V_VCC_3.3: Q3.3 (D), R113.2; also elsewhere on the board
7.CAM0_C_N: J2.40; also elsewhere on the board
7.CAM0_C_P: J2.42; also elsewhere on the board
7.CAM0_D1_N: J2.28; also elsewhere on the board
7.CAM0_D1_P: J2.30; also elsewhere on the board
7.CAM0_D2_N: J2.34; also elsewhere on the board
7.CAM0_D2_P: J2.36; also elsewhere on the board
7.CAM1_C_N: J2.27; also elsewhere on the board
7.CAM1_C_P: J2.29; also elsewhere on the board
7.CAM1_D1_N: J2.15; also elsewhere on the board
7.CAM1_D1_P: J2.17; also elsewhere on the board
7.CAM1_D2_N: J2.21; also elsewhere on the board
7.CAM1_D2_P: J2.23; also elsewhere on the board
7.CAM1_D3_N: J2.33
7.CAM1_D3_P: J2.35
7.CAM1_D4_N: J2.39
7.CAM1_D4_P: J2.41
7.GPIO2_GPIO: J8.58; also elsewhere on the board
7.GPIO3_GPIO: J8.56; also elsewhere on the board
7.GPIO4_GPIO: J8.54; also elsewhere on the board
7.GPIO5_GPIO: J8.34; also elsewhere on the board
7.GPIO6_GPIO: J8.30; also elsewhere on the board
7.GPIO7_GPIO: J8.37; also elsewhere on the board
7.I2C0_SCL: J8.80; also elsewhere on the board
7.I2C0_SDA: J8.82; also elsewhere on the board
7.I2C_ID_SCL: J8.35; also elsewhere on the board
7.I2C_ID_SDA: J8.36; also elsewhere on the board
7.PCIE_CLKREQ_GPIO: J2.2, R9.1
7.PCIE_NRESET: J2.9; also elsewhere on the board
7.UART0_RXD: J8.51; also elsewhere on the board
7.UART0_TXD: J8.55; also elsewhere on the board
7.UART4_4W_CTS: J8.44; also elsewhere on the board
7.UART4_4W_RTS: J8.38; also elsewhere on the board
7.UART4_4W_RXD: J8.40; also elsewhere on the board
7.UART4_4W_TXD: J8.39; also elsewhere on the board
7.VLOGIC_VLOGIC: R113.1; also elsewhere on the board
14.5.0V_VCC_5.0: J8.77, J8.79, J8.81, J8.83, J8.85, J8.87; also elsewhere on the board
!EXTRST$7: J8.100, Q5.1 (G), R103.2
!RPIBOOT$7: J8.93; also elsewhere on the board
CORAL_D_N: J2.3; also elsewhere on the board
CORAL_D_P: J2.5; also elsewhere on the board
DS_LOAD$7: Q3.2 (S), Q4.2 (S)
DS_LOAD_1V8$7: Q1.2 (S), Q6.2 (S)
EEPROM_!WP: J8.20
ETH_SYNC_IN: J8.16
ETH_SYNC_OUT: J8.18
GLOBAL_EN: J8.99
GND: J2.7, J2.8, J2.13, J2.14, J2.19, J2.20, J2.25, J2.26, J2.31, J2.32, J2.37, J2.38, J2.44, J2.50, J2.55, J2.56, J2.61, J2.62, J2.67, J2.68, J2.73, J2.74, J2.79, J2.80, J2.85, J2.86, J2.91, J2.92, J2.97, J2.98, J8.1, J8.2, J8.7, J8.8, J8.13, J8.14, J8.22, J8.23, J8.32, J8.33, J8.42, J8.43, J8.52, J8.53, J8.59, J8.60, J8.65, J8.66, J8.71, J8.74, J8.98, MP1.1, MP2.1, MP3.1, MP4.1, Q5.2 (S), R9.2, R42.2, R103.1; also elsewhere on the board
GPIO_VREF$7: J8.78, R101.2, R106.2; also elsewhere on the board
LOAD_GATE$7: Q1.1 (G), Q3.1 (G), Q4.1 (G), Q5.3 (D), Q6.1 (G)
PCIE_CLK_N: J2.12; also elsewhere on the board
PCIE_CLK_P: J2.10; also elsewhere on the board
PCIE_RX_N: J2.18; also elsewhere on the board
PCIE_RX_P: J2.16; also elsewhere on the board
PCIE_TX_N: J2.24; also elsewhere on the board
PCIE_TX_P: J2.22; also elsewhere on the board
PI_!LED_ACT: J8.21
PI_LED_!PWR: J8.95
SD_PWR_ON: J8.75
SD_VDD_OV: J8.73
USB_OTG_ID: J2.1, R42.1
VDAC_COMP: J2.11

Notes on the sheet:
Raspberry Pi CM4
GPIO
High Speed

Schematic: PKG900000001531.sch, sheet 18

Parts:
C6: 0.1uF; 0201
IC1: CAT24C256YI-G; TSSOP8
R8, R104, R105: 100K 1%; 0201
R10, R20, R110: 1K5; 0201
S2: EVQ; KMT0

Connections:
7.I2C_ID_SCL: IC1.6 (SCL), R10.1; also elsewhere on the board
7.I2C_ID_SDA: IC1.5 (SDA), R110.1; also elsewhere on the board
!RPIBOOT$7: S2.3 (B), S2.4 (B'); also elsewhere on the board
A0$7: IC1.1 (A0), R8.2
A1$7: IC1.2 (A1), R105.2
A2$7: IC1.3 (A2), R104.2
GND: C6.2, IC1.4 (GND), IC1.7 (WP), R20.1, R104.1, R105.1; also elsewhere on the board
GPIO_VREF$7: C6.1, IC1.8 (VCC), R8.1, R10.2, R110.2; also elsewhere on the board
RPIBOOT_SWITCH$19: R20.2, S2.1 (A), S2.2 (A')

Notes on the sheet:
Raspberry Pi CM4

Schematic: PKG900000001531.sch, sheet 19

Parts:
R1, R3, R52, R54: 0R; 0201
R2, R4: DNP; 0201

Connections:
7.UART4_4W_CTS: R2.1, R3.1; also elsewhere on the board
7.UART4_4W_RTS: R1.1, R4.1; also elsewhere on the board
7.UART4_4W_RXD: R54.1; also elsewhere on the board
7.UART4_4W_TXD: R52.1; also elsewhere on the board
UART5_CTS_TELEM2: R1.2, R2.2; also elsewhere on the board
UART5_RTS_TELEM2: R3.2, R4.2; also elsewhere on the board
UART5_RX_TELEM2: R52.2; also elsewhere on the board
UART5_TX_TELEM2: R54.2; also elsewhere on the board

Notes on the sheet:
HART-HART Bridge

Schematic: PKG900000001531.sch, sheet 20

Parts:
J9: CON8X3STD; MA08-3W-0100
R29, R30, R32, R33, R34, R35, R36, R37: 220R; 0402
U17, U18: TPD4E02B0410-USON; UFDFN-10

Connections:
1.PWM1_PWM_: J9.17, R29.2
1.PWM2_PWM_: J9.18, R30.2
1.PWM3_PWM_: J9.19, R32.2
1.PWM4_PWM_: J9.20, R33.2
1.PWM5_PWM_: J9.21, R34.2
1.PWM6_PWM_: J9.22, R35.2
1.PWM7_PWM_: J9.23, R36.2
1.PWM8_PWM_: J9.24, R37.2
5V_HIGH: J9.9, J9.10, J9.11, J9.12, J9.13, J9.14, J9.15, J9.16; also elsewhere on the board
FMU_CH1: R29.1, U18.5 (P4), U18.6 (P4); also elsewhere on the board
FMU_CH2: R30.1, U18.4 (P3), U18.7 (P3); also elsewhere on the board
FMU_CH3: R32.1, U18.2, U18.9 (P2); also elsewhere on the board
FMU_CH4: R33.1, U18.1, U18.10 (P1); also elsewhere on the board
FMU_CH5: R34.1, U17.5 (P4), U17.6 (P4); also elsewhere on the board
FMU_CH6: R35.1, U17.4 (P3), U17.7 (P3); also elsewhere on the board
FMU_CH7: R36.1, U17.2, U17.9 (P2); also elsewhere on the board
FMU_CH8: R37.1, U17.1, U17.10 (P1); also elsewhere on the board
GND: J9.1, J9.2, J9.3, J9.4, J9.5, J9.6, J9.7, J9.8, U17.3 (SHIELD), U17.8 (SHIELD), U18.3 (SHIELD), U18.8 (SHIELD); also elsewhere on the board

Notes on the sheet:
Octal Servo

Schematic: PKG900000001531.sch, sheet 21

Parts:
J10: FPC-15VERT; 1-1734248-5

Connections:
2.3.3V_VCC_3.3: J10.1_15 (15); also elsewhere on the board
7.CAM0_C_N: J10.1_8 (8); also elsewhere on the board
7.CAM0_C_P: J10.1_9 (9); also elsewhere on the board
7.CAM0_D1_N: J10.1_2 (2); also elsewhere on the board
7.CAM0_D1_P: J10.1_3 (3); also elsewhere on the board
7.CAM0_D2_N: J10.1_5 (5); also elsewhere on the board
7.CAM0_D2_P: J10.1_6 (6); also elsewhere on the board
7.GPIO4_GPIO: J10.1_11 (11); also elsewhere on the board
7.I2C_ID_SCL: J10.1_13 (13); also elsewhere on the board
7.I2C_ID_SDA: J10.1_14 (14); also elsewhere on the board
GND: J10.1_1 (1), J10.1_4 (4), J10.1_7 (7), J10.1_10 (10); also elsewhere on the board

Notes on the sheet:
RPi CSI Vertical Connector

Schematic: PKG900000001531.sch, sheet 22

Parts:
J11: FPC-15VERT; 1-1734248-5

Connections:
2.3.3V_VCC_3.3: J11.1_15 (15); also elsewhere on the board
7.CAM1_C_N: J11.1_8 (8); also elsewhere on the board
7.CAM1_C_P: J11.1_9 (9); also elsewhere on the board
7.CAM1_D1_N: J11.1_2 (2); also elsewhere on the board
7.CAM1_D1_P: J11.1_3 (3); also elsewhere on the board
7.CAM1_D2_N: J11.1_5 (5); also elsewhere on the board
7.CAM1_D2_P: J11.1_6 (6); also elsewhere on the board
7.GPIO5_GPIO: J11.1_11 (11); also elsewhere on the board
7.I2C0_SCL: J11.1_13 (13); also elsewhere on the board
7.I2C0_SDA: J11.1_14 (14); also elsewhere on the board
GND: J11.1_1 (1), J11.1_4 (4), J11.1_7 (7), J11.1_10 (10); also elsewhere on the board

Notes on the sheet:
RPi CSI Vertical Connector

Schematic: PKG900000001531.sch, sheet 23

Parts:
J12: JST-GH-6H

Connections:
5V_PERIPHERAL: J12.P1; also elsewhere on the board
GND: J12.P6; also elsewhere on the board
I2C1_SCL_BASE_GPS1_MAG_LED_PM1: J12.P4; also elsewhere on the board
I2C1_SDA_BASE_GPS1_MAG_LED_PM1: J12.P5; also elsewhere on the board
USART1_RX_GPS1: J12.P3; also elsewhere on the board
USART1_TX_GPS1: J12.P2; also elsewhere on the board

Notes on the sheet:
JST GH 6-pin (GPS) Header

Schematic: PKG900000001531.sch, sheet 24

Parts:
J13: JST-GH-6H

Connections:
13.VCC_VCC_5.0: J13.P1, J13.P2; also elsewhere on the board
ADC3_3V3: J13.P4; also elsewhere on the board
ADC3_6V6: J13.P3; also elsewhere on the board
GND: J13.P5, J13.P6; also elsewhere on the board

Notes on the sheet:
JST GH 6-pin (Power) Header

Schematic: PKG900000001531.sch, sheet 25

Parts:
C270: 0.01uF; 0201
R6, R111: 24K; 0201
R7: 22K; 0201
R112: 0R; 0201
R114, R115: 5K; 0201
U105: TPS2121; VQFN12-HR

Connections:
3.5.0V_VCC_5.0: R111.2, U105.7 (IN1); also elsewhere on the board
13.VCC_VCC_5.0: R6.2, U105.2 (IN2); also elsewhere on the board
14.5.0V_VCC_5.0: U105.1 (OUT), U105.8 (OUT); also elsewhere on the board
GND: C270.2, R7.1, R112.1, R114.1, R115.1, U105.3 (CP2), U105.9 (ST), U105.12 (GND); also elsewhere on the board
ILUM$14: R7.2, U105.10 (ILM)
OV1$14: R111.1, R114.2, U105.5 (OV1)
OV2$14: R6.1, R115.2, U105.4 (OV2)
PR1$14: R112.2, U105.6 (PR1)
SS$14: C270.1, U105.11 (SS)

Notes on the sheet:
TI TPS2121 Power Source Muxer

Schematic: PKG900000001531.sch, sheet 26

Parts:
J14: JST-GH-4H

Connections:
5V_PERIPHERAL: J14.P1; also elsewhere on the board
18.CAN_HL_CAN_H: J14.P2; also elsewhere on the board
18.CAN_HL_CAN_L: J14.P3; also elsewhere on the board
GND: J14.P4; also elsewhere on the board

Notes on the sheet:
JST GH 4-pin (CAN) Header

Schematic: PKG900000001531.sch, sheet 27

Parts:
J1: JST-GH-5H

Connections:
3V3_SPEKTRUM: J1.P4; also elsewhere on the board
5V_PERIPHERAL: J1.P1; also elsewhere on the board
FMU_PPM_INPUT: J1.P3; also elsewhere on the board
GND: J1.P5; also elsewhere on the board
USART6_RX_FROM_IO__RC_INPUT: J1.P2; also elsewhere on the board

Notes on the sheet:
JST GH 5-pin (RC) Header

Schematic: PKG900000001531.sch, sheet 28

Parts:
C16, C27, C34, C38, C72: 0.1uF; 0201
C28: 10uF; 0603
C40: 1000pF; 0201
C41: 270pF; 0201
R19, R43, R58: 0R; 0201
R21, R48: 10K 1%; 0201
R27, R28: 1K5; 0201
R49: 14K7; 0201
R50: 100K 1%; 0201
U5: G313-06329-00
U6: NCP308; WDFN6
U19: TXS0104E; S-PVQFN-N14

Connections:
7.1.8V_VCC_1.8: C34.1, R19.2, R21.2, R27.2, R28.2, R48.2, U5.54 (AON), U19.1 (VCCA), U19.8 (OE); also elsewhere on the board
7.3.3V_VCC_3.3: C27.1, C28.1, C38.1, R50.2, U5.56 (VIN), U5.57 (VIN), U5.58 (VIN), U5.59 (VIN), U5.60 (VIN), U5.61 (VIN), U5.62 (VIN), U5.63 (VIN), U5.64 (VIN), U5.65 (VIN), U5.66 (VIN), U5.67 (VIN), U6.1 (VDD), U19.14 (VCCB); also elsewhere on the board
7.GPIO2_GPIO: U19.11 (B3); also elsewhere on the board
7.GPIO3_GPIO: U19.10 (B4); also elsewhere on the board
7.GPIO6_GPIO: U19.12 (B2); also elsewhere on the board
7.GPIO7_GPIO: U19.13 (B1); also elsewhere on the board
!RST$17: R48.1, U5.76 (!RST), U6.6 (!RESET)
CT1$17: C41.1, U6.3 (CT)
GND: C27.2, C28.2, C34.2, C38.2, C40.2, C41.2, R43.1, R49.1, R58.1, U5.1 (GND), U5.2 (GND), U5.3 (GND), U5.6 (GND), U5.9 (GND), U5.12 (GND), U5.15 (GND), U5.16 (GND), U5.17 (GND), U5.18 (GND), U5.19 (GND), U5.20 (GND), U5.21 (GND), U5.22 (GND), U5.23 (GND), U5.24 (GND), U5.25 (GND), U5.26 (GND), U5.27 (GND), U5.28 (GND), U5.29 (GND), U5.30 (GND), U5.31 (GND), U5.32 (GND), U5.33 (GND), U5.34 (GND), U5.35 (GND), U5.36 (GND), U5.38 (GND), U5.39 (GND), U5.40 (GND), U5.41 (GND), U5.42 (GND), U5.43 (GND), U5.44 (GND), U5.45 (GND), U5.46 (GND), U5.47 (GND), U5.48 (GND), U5.51 (GND), U5.55 (GND), U5.68 (GND), U5.69 (GND), U5.70 (GND), U5.71 (GND), U5.72 (GND), U5.73 (GND), U5.74 (GND), U5.75 (GND), U5.79 (GND), U5.80 (GND), U5.81 (GND), U5.86 (GND), U5.87 (GND), U5.88 (GND), U5.89 (GND), U5.90 (GND), U5.91 (GND), U5.92 (GND), U5.93 (GND), U5.94 (GND), U5.95 (GND), U5.96 (GND), U5.97 (GND), U5.98 (GND), U5.99 (GND), U5.100 (GND), U5.101 (GND), U5.102 (GND), U5.103 (GND), U5.104 (GND), U5.105 (GND), U5.106 (GND), U5.107 (GND), U5.108 (GND), U5.109 (GND), U5.110 (GND), U5.111 (GND), U5.112 (GND), U5.113 (GND), U5.114 (GND), U5.115 (GND), U5.116 (GND), U5.117 (GND), U5.118 (GND), U5.119 (GND), U5.120 (GND), U6.5 (GND), U6.EPAD (GND), U19.7 (GND); also elsewhere on the board
I2C_SCL: R27.1, U5.50 (RESERVED), U19.5 (A4)
I2C_SDA: R28.1, U5.49 (RESERVED), U19.4 (A3)
PGOOD4$17: U5.37 (PGOOD4), U6.4 (!MR)
PHY_PRG: U5.84 (RESERVED), U19.2 (A1)
PMIC_EN$17: R21.1, U5.53 (PMIC_EN), U19.3 (A2)
SD_ALRM$17: U5.82 (SD_ALRM)
SENSE$17: C40.1, R49.2, R50.1, U6.2 (SENSE)
USB1_N: U5.14 (USB2_D_N); also elsewhere on the board
USB1_P: U5.13 (USB2_D_P); also elsewhere on the board
USB1_SSRX_N: U5.4 (PCIE_TX_N); also elsewhere on the board
USB1_SSRX_P: U5.5 (PCIE_TX_P); also elsewhere on the board
USB1_SSTX_N: C16.2; also elsewhere on the board
USB1_SSTX_P: C72.2; also elsewhere on the board
USB1_SSTX__N: C16.1, U5.7 (PCIE_RX_P)
USB1_SSTX__P: C72.1, U5.8 (PCIE_RX_N)
USB_SEL$17: R19.1, U5.83 (USB_SEL)
_PCIE_CLK_N: R43.2, U5.10 (PCIE_REFCLK_N)
_PCIE_CLK_P: R58.2, U5.11 (PCIE_REFCLK_P)

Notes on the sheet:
Google Coral G313-06329-00 Accelerator

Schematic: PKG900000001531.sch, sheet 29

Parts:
C2: 4.7nF; 0201
C3, C271: 0.1uF; 0201
R117: 10K 1%; 0201
RT4, RT5: 60R4; 0805
U2: TJA1051TK/3; HVSON8

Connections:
2.3.3V_VCC_3.3: C3.1, U2.5 (VIO); also elsewhere on the board
5V_PERIPHERAL: C271.1, U2.3 (VCC); also elsewhere on the board
18.CAN_HL_CAN_H: RT4.2, U2.7 (CANH); also elsewhere on the board
18.CAN_HL_CAN_L: RT5.1, U2.6 (CANL); also elsewhere on the board
CAN1_RX: U2.4 (RXD); also elsewhere on the board
CAN1_TX: U2.1 (TXD); also elsewhere on the board
CAP$18: C2.1, RT4.1, RT5.2
GND: C2.2, C3.2, C271.2, R117.1, U2.2 (GND), U2.P$1 (FLAG), U2.P$2 (FLAG), U2.P$3 (FLAG), U2.P$4 (FLAG), U2.P$5 (FLAG), U2.P$6 (FLAG), U2.P$8 (FLAG), U2.P$9 (FLAG); also elsewhere on the board
SEL$18: R117.2, U2.8 (S)

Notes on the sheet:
NXP TJA1051TK/3 CAN Transceiver

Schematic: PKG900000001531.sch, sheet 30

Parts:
C1: 47pF; 0201
D1: B72590D50A060; D0402
R119: 10K 1%; 0201
R120: 150R; 0201
S1: EVQ

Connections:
2.3.3V_VCC_3.3: R119.2; also elsewhere on the board
BTN_A$22: D1.P2, R119.1, R120.1, S1.B@1 (B), S1.B@2 (B')
GND: C1.2, D1.P1, S1.A@1 (A), S1.A@2 (A'); also elsewhere on the board
NRST: C1.1, R120.2; also elsewhere on the board

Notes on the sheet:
Pushbutton

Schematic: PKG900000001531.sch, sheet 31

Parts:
C14: 0.1uF; 0201
C15: 10uF; 0603
J3: USD_WURTH; USD
RP2: 33R0; 741X16
RP3: 100K0; 741X16

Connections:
1.SD_CARD_POWER: C14.1, C15.1, J3.4 (VDD), RP3.1, RP3.2, RP3.3, RP3.4, RP3.5, RP3.6; also elsewhere on the board
3V_MMC_CLK$24: J3.5 (CLK/SCLK), RP2.15
3V_MMC_CMD$24: J3.3 (CMD/DI), RP2.16
3V_MMC_D0$24: J3.7 (DAT0/DO), RP2.14
3V_MMC_D1$24: J3.8 (DAT1/RSV), RP2.13
3V_MMC_D2$24: J3.1 (DAT2/RSV), RP2.12
3V_MMC_D3$24: J3.2 (DAT3_CD/CS), RP2.11
GND: C14.2, C15.2, J3.6 (GND); also elsewhere on the board
SDMMC2_CLK: RP2.2; also elsewhere on the board
SDMMC2_CMD: RP2.1, RP3.16; also elsewhere on the board
SDMMC2_D0: RP2.3, RP3.14; also elsewhere on the board
SDMMC2_D1: RP2.4, RP3.13; also elsewhere on the board
SDMMC2_D2: RP2.5, RP3.12; also elsewhere on the board
SDMMC2_D3: RP2.6, RP3.11; also elsewhere on the board

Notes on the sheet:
SD Card

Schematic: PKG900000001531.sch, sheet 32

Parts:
C32: 10pF; 0201
C73, C74, C75, C76, C77, C78, C79, C82, C83, C84, C85, C86, C88, C89, C92, C93: 0.1uF; 0201
C90, C91: 4.7uF / 16V; 0603
C94: 6.8nF; 0201
C158, C167: 10uF; 0603
R11: 12K1; 0201
R69, R70: 10K 1%; 0201
U4: ASM1142; QFN64-9X9MM-FT2232HQ
U12: ADP1740ACPZ-1.2-R7; LFCSPWQ16
Y5: 20.000MHz; CRYSTAL-3225

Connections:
2.3.3V_VCC_3.3: C73.1, C76.1, C77.1, C85.1, C86.1, C88.1, C158.1, R69.2, R70.2, U4.4 (VCC), U4.20 (VCCSUS), U4.24 (VCCSUS), U4.32 (VCC), U4.38 (VCCU), U4.44 (VCCU), U4.55 (VCCP), U4.62 (VCCP), U12.1 (VIN), U12.2 (VIN), U12.3 (VIN), U12.4 (EN), U12.15 (VIN), U12.16 (VIN); also elsewhere on the board
7.PCIE_NRESET: R69.1, U4.30 (!PERST); also elsewhere on the board
!INT: U4.2 (!SMI)
!PCIE_WAKE: U4.25 (!PEWAKE)
!RST$: R70.1, U4.9 (!PORST)
!SPI_CS$: U4.7 (!SPI_CS)
!USB1_NOC: U4.28 (!OC1)
!USB2_NOC: U4.29 (!OC2)
GND: C73.2, C74.2, C75.2, C76.2, C77.2, C78.2, C79.2, C82.2, C83.2, C84.2, C85.2, C86.2, C88.2, C89.2, C90.2, C91.2, C94.2, C158.2, C167.2, R11.1, U4.15 (GND), U4.65 (GND), U4.EPAD1 (GND), U4.EPAD2 (GND), U4.EPAD3 (GND), U4.EPAD4 (GND), U4.EPAD5 (GND), U4.EPAD6 (GND), U4.EPAD7 (GND), U4.EPAD8 (GND), U4.EPAD9 (GND), U4.EPAD10 (GND), U4.EPAD11 (GND), U4.EPAD12 (GND), U12.6 (GND), U12.EP (GND), U12.EP1 (GND), U12.EP2 (GND), U12.EP3 (GND), U12.EP4 (GND), Y5.2, Y5.4; also elsewhere on the board
PCIE_CLK_N: U4.49 (PCIE_REFCLK_N); also elsewhere on the board
PCIE_CLK_P: U4.48 (PCIE_REFCLK_P); also elsewhere on the board
PCIE_RX0__N: C93.2, U4.57 (PCIE_TX0_N)
PCIE_RX0__P: C92.2, U4.56 (PCIE_TX0_P)
PCIE_RX_N: C92.1; also elsewhere on the board
PCIE_RX_P: C93.1; also elsewhere on the board
PCIE_TX_N: U4.53 (PCIE_RX0_P); also elsewhere on the board
PCIE_TX_P: U4.54 (PCIE_RX0_N); also elsewhere on the board
REXT$: R11.2, U4.59 (REXT)
SPI_CLK$: U4.5 (SPI_CLK)
SPI_DI$: U4.8 (SPI_DI)
SPI_DO$: U4.6 (SPI_DO)
UART_RX$: U4.10 (UART_RX)
UART_TX$: U4.11 (UART_TX)
USB1_N: U4.22 (USB1_N); also elsewhere on the board
USB1_P: U4.23 (USB1_P); also elsewhere on the board
USB1_PWREN: U4.26 (PWRON1)
USB1_SSRX_N: U4.46 (USB1_SSRX_N); also elsewhere on the board
USB1_SSRX_P: U4.45 (USB1_SSRX_P); also elsewhere on the board
USB1_SSTX_N: U4.43 (USB1_SSTX_N); also elsewhere on the board
USB1_SSTX_P: U4.42 (USB1_SSTX_P); also elsewhere on the board
USB2_N: U4.18 (USB2_N)
USB2_P: U4.19 (USB2_P)
USB2_PWREN: U4.27 (PWRON2)
USB2_SSRX_N: U4.37 (USB2_SSRX_N)
USB2_SSRX_P: U4.36 (USB2_SSRX_P)
USB2_SSTX_N: U4.40 (USB2_SSTX_N)
USB2_SSTX_P: U4.39 (USB2_SSTX_P)
V1.2$: C74.1, C75.1, C78.1, C79.1, C82.1, C83.1, C84.1, C89.1, C90.1, C91.1, C167.1, U4.1 (VDD), U4.12 (VDD), U4.21 (VDDSUS), U4.33 (VDD), U4.34 (VDDSUS), U4.35 (VDDU), U4.41 (VDDU), U4.47 (VDDU), U4.52 (VDDP), U4.58 (VDDP), U12.9 (SENSE), U12.10 (VOUT), U12.11 (VOUT), U12.12 (VOUT), U12.13 (VOUT), U12.14 (VOUT)
VCC1V1_SS$: C94.1, U12.7 (SS)
XI$: C32.2, U4.51 (XI), Y5.1
XO$: C32.1, U4.50 (XO), Y5.3

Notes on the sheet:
PCIe to USB3.0

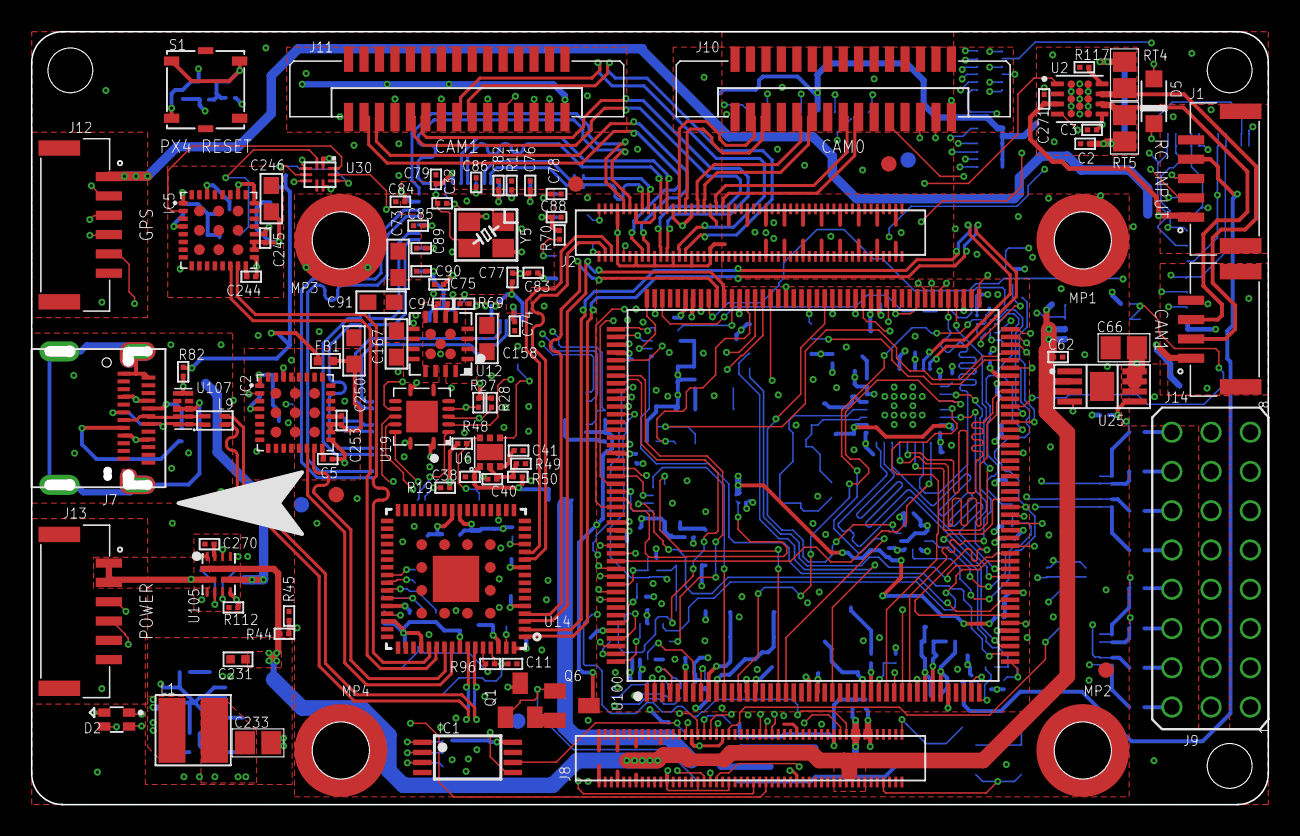
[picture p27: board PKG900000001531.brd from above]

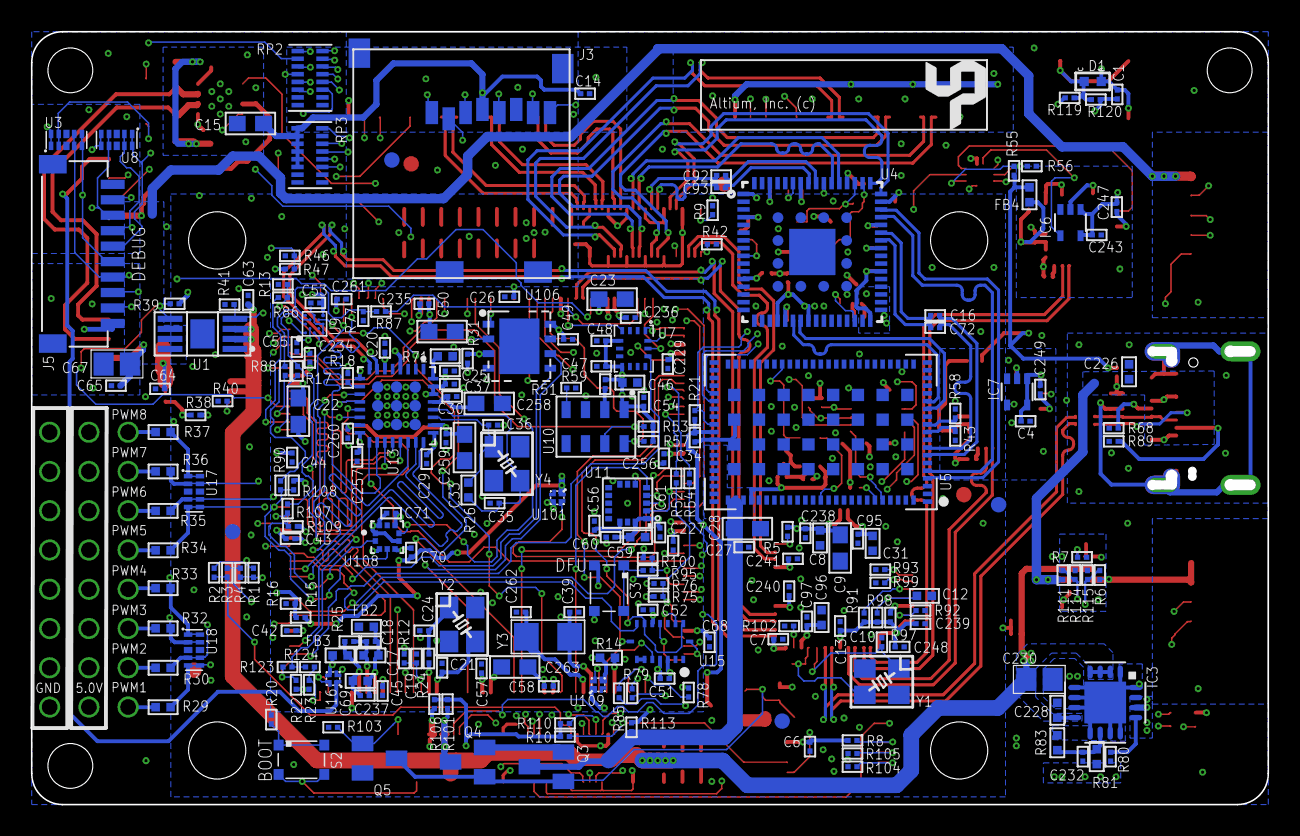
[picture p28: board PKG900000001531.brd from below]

Board: 6 copper layers, 80.0 x 50.0 mm, 326 parts (228 on the bottom side), 283 nets.

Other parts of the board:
U$53, U$55, U$60: DNP; GEPPETTO_HOLE_2.9

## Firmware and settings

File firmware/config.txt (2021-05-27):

# For more options and information see
# http://rpf.io/configtxt
# Some settings may impact device functionality. See link above for details

# uncomment if you get no picture on HDMI for a default "safe" mode
#hdmi_safe=1

# uncomment this if your display has a black border of unused pixels visible
# and your display can output without overscan
#disable_overscan=1

# uncomment the following to adjust overscan. Use positive numbers if console
# goes off screen, and negative if there is too much border
#overscan_left=16
#overscan_right=16
#overscan_top=16
#overscan_bottom=16

# uncomment to force a console size. By default it will be display's size minus
# overscan.
#framebuffer_width=1280
#framebuffer_height=720

# uncomment if hdmi display is not detected and composite is being output
#hdmi_force_hotplug=1

# uncomment to force a specific HDMI mode (this will force VGA)
#hdmi_group=1
#hdmi_mode=1

# uncomment to force a HDMI mode rather than DVI. This can make audio work in
# DMT (computer monitor) modes
#hdmi_drive=2

# uncomment to increase signal to HDMI, if you have interference, blanking, or
# no display
#config_hdmi_boost=4

# uncomment for composite PAL
#sdtv_mode=2

#uncomment to overclock the arm. 700 MHz is the default.
#arm_freq=800

# Uncomment some or all of these to enable the optional hardware interfaces
#dtparam=i2c_arm=on
#dtparam=i2s=on
#dtparam=spi=on

# Uncomment this to enable infrared communication.
#dtoverlay=gpio-ir,gpio_pin=17
#dtoverlay=gpio-ir-tx,gpio_pin=18

# Additional overlays and parameters are documented /boot/overlays/README

# Enable audio (loads snd_bcm2835)
dtparam=audio=on

[pi4]
# Enable DRM VC4 V3D driver on top of the dispmanx display stack
dtoverlay=vc4-fkms-v3d
max_framebuffers=2

[all]
#dtoverlay=vc4-fkms-v3d

# pixhawk
enable_uart=1
dtoverlay=dwc2,dr_mode=host
start_x=1
gpu_mem=128
dtoverlay=uart4,ctsrts
dtoverlay=pcie-32bit-dma
gpio=6,7=op,dh

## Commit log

2020-10-18 Added hardware documents for revision 1.
    [PKG900000001531.brd, PKG900000001531.sch]
2020-12-01 Update hardware files for revision 2.
    [PKG900000001531.brd, PKG900000001531.sch]
2021-04-15 Update firmware to use upstream Raspberry Pi OS images and outline changes necessary to use cameras and onboard telemetry.
    [config.txt]
2021-05-27 Update board design files to v4.
    Add ROS2 and Coral support information to the firmware docs.
    [PKG900000001531.brd, PKG900000001531.sch, config.txt]
